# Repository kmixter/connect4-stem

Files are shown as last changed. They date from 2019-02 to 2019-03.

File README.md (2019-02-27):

# README #

This repository is the software and 3D part source for a "Connect-4" STEM project.

### Parts to purchase ###

* Purchase [wooden Connect Four game](https://www.target.com/p/connect-4-rustic-series-board-game/-/A-52118927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) for $19
* Purchase [aluminum slider](https://www.sparkfun.com/products/12500) for $12
* Purchase [channel slider](https://www.sparkfun.com/products/12560) for $5
* Purchase 2 [ball bearings](https://www.sparkfun.com/products/13277) for $2
* Purchase [stepper motor](https://www.amazon.com/gp/product/B00EYIFW70/ref=ppx_yo_dt_b_asin_title_o07__o00_s00?ie=UTF8&psc=1) for $17
* Purchase [Induino Mega](https://www.amazon.com/gp/product/B01G6Z1EYI/ref=ppx_yo_dt_b_asin_title_o04__o00_s00?ie=UTF8&psc=1) for $14 (or any Arduino Mega compatible board)
* Purchase [Adafruit motor shield](https://www.amazon.com/gp/product/B00PUTH3B0/ref=oh_aui_search_asin_title?ie=UTF8&psc=1) for $19
* Purchase [Timing belt, pulley, and tensioner](https://www.amazon.com/gp/product/B07FYYGFGQ/ref=ppx_yo_dt_b_asin_title_o09__o00_s00?ie=UTF8&psc=1) for $13
* Purchase [Stacking headers](https://www.amazon.com/gp/product/B00LB76EVU/ref=ppx_yo_dt_b_asin_title_o00__o00_s00?ie=UTF8&psc=1) for $6
* Purchase [Ribbon cable](https://www.amazon.com/gp/product/B01D9KISHY/ref=ppx_yo_dt_b_asin_title_o09__o00_s01?ie=UTF8&psc=1) for $8
* Purchase [LCD screen](https://www.amazon.com/gp/product/B01E6N19YC/ref=ppx_yo_dt_b_asin_title_o07__o00_s00?ie=UTF8&psc=1) for $10
* Purchase [Servo](https://www.amazon.com/gp/product/B07C5PGD3Q/ref=oh_aui_search_asin_title?ie=UTF8&psc=1) for $11
* Purchase 7 [photo interrupters](https://www.digikey.com/product-detail/en/sharp-socle-technology/GP1A57HRJ00F/1855-1043-ND/718287) for $28
* Purchase [red](https://www.adafruit.com/product/1445) and [green](https://www.adafruit.com/product/1504) momentary pushbuttons for $2
* Purchase 7 330ohm 1/4w resistors
* Purchase a micro-switch
* Purchase a [battery and charger](https://www.overstock.com/Emergency-Preparedness/Large-Capacity-9800MAH-DC12V-Portable-Rechargeable-Li-ion-Battey-Pack/17432557/product.html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) for $30

* You will need a 3D printer and filament. We used ABS, though presumably PLA also works.
* You will also want wood screws of various sizes and metal bolt/nut combos, mostly of 3mm size.
* For nicer connections, you'll also want to consider soldering iron/solder, heat shrink, and a Dupont connector kit.

### Construction of robot ###

The following parts are all available here print. They can be printed on
an inexpensive hobbyist 3D printer with a 150mm x 150mm x 150mm printing
volume. We used ABS filament for durability and easy in welding pieces
together with acetone. No acrylic parts are needed.

These are the parts for the gantry dropper mechanism above the board:

* [gantry hopper holder](parts/PatrickMcCabe/Piece Holder.STL)
* [2x belt clamp](parts/PatrickMcCabe/Belt Clamp.STL)
* [gantry slider top](parts/PatrickMcCabe/Slider Top.STL)
* [2x bearing block](parts/PatrickMcCabe/Bearing Block.STL)
* [Motor mount](parts/PatrickMcCabe/Motor Mount.STL)
* [Combined idler and post](parts/combined-idler-post.stl)
* [Disc Funnel](parts/PatrickMcCabe/Slider Spacer Front.STL)
* [Servo Releaser](parts/thinner-servo-releaser.stl)
* [Disc hopper](parts/taller-gantry-hopper.stl)

To build the gantry, which is the slider that slides across the top of
the board and drops discs into the board:

* Connect the stepper motor to the Motor Mount with screws.
* Connect the motor mount to the 15" C channel in the second to left-most
  screw holes.
* Insert the bearings into the two bearing blocks. This is a very tight
  fit. I used a pair of pliers to squeeze the bearing into the block to be
  flush. This damaged one of my bearings and I needed to purchase a new one.
  Be careful to only squeeze the outermost ring of the bearing to avoid bending
  the internal mechanism and causing friction when the bearing moves.
* Insert the combined idler and rod into the two bearings.
* Screw the two bearing blocks into the C channel, aligned with the rightmost
  screw holes. The bearing blocks did not fit well into the channel and would
  cause the channel to bend outward and increase the friction of the slider
  against the channel. I ended up significantly sanding down the two bearing
  blocks so they fit into the channel without bending it. Sorry I did not get
  around to redesigning the parts to be smaller. Likely they are about 1mm too
  thick.
* Place the C clamps on the C-channel.
* Screw the top of the C clamps into the gantry slider top.
* Screw the front of the C clamps into the disc funnel.
* Screw the gantry hopper holder into the left side of the C clamps.
* Screw the servo onto the top of the gantry slider top.
* Cut the servo arm to be less than 4mm and screw the Servo Releaser
  into the servo arm.
* Superglue the servo arm onto the servo drive to avoid accidental disloding.
* Screw the gantry hopper into the gantry hopper holder.
* Attach the belt pulley to the stepper motor with set screw included with
  pulley.
* Wrap the belt drive around the idler and the stepper pulley, pull moderately tight.
* Cut belt to 15cm longer than distance to gantry slider top.
* Route the top sides of the belt loop up into the gantry slider top, pulled around
  to the outside of the gantry slider top.
* Clamp down the belt drive with 2 Belt Clamps and 4 screws.
* Tighten the belts with spring tensioners.
* Connect the microswitch to the C channel. See picture for positioning.
* Consider soldering a 3-pin connector like that shown to the microcontroller
  to make it easier to take the device apart in the future.

At this point the next best step is to attach the 7 photo-interrupters to
the top of the board. This is probably the most labor intensive step. Each
photo-interrupter has an emitter side (2 pins) and a phototransistor side (3
pins). On both sides longest lead is ground. The middle lead of the phototransistor
is the output. The other lead is VCC. Since the emitter is just a simple
IR LED, current limiting is required to avoid burning out the LED. Each
LED power needs a 330V 1/4W resistor between it and actual 5V input. The
phototransistor is actually a complicated circuit and does not need current
limiting.

The photo-interrupters come with emitter and receiver sides connected by a
plastic spacer. This spacer is similar to the width of the Connect 4 board,
so it is tempting to think they can just be used as is. However, the spacer
is too thick and discs will not fit through the spacers (they would leave
less than 1 1/4" wide, the diameter of the discs). As such, the photo-interruptors
call be cut easily with wire cutters to give full access to the drop area
at the top of the board.

But before cutting the photo-interrupters they should be wired up and attached
to the board. In my case I put the phototransistor side at the back of the board
(since we need 7 signal wires coming out from the back of the board, which is
unsightly), and emitter side at the front. For the emitter and phototransistors,
the same GND and 5V wires were used. These wires plus the 7 signal wires come
from the same ribbon cable. For convenience I used white wire for 5V, black for GND,
and purple through brown for the 7 columns, using 9 of the 10 wires of the 10-wire
ribbon cable. Additionally, the 5V and GND side of the microswitch and its output
should be connected to this cable. The output signal should be wired to gray.

A bus wire was used to solder all GND connections together. On the emitter side
since all emitters require 330ohm biasing resistors I used heat-shrink to hide
the resistors and insulate the 5V wire which was chained between each emitter
positive side.

To reduce surplus wiring in this visible part of the board, I used a paper template
of the top of the board, with exact markings of each column and spaced, soldered,
and heat-shrunk the wires for the photo-interruptors. The spacer of the
photo-transistors was still intact at this stage. Finally when all wires were
intact and connected to the 10-wire ribbon cable, the spacers were cut for all 7
interruptors. The photo-interrupters were then glued to the top of the board
with a hotglue gun. When glued, make sure that the emitter and receiver sides of
the photo-interrupters are as flush as possible with the opening of the board.
If they are too wide, discs can get stuck on the top of the board when they pass
them. If they are too narrow, discs can get stuck on top of the photo interrupter.
Any excess glue towards the inside of the board can be clipped away for a smooth
transition from the funnel, past photo-interrupter, into the board.

Next the feet and slide should be printed and attached to the board.

Print these parts:

* [back-right foot](parts/foot.stl)
* [back-left battery-holder foot](parts/battery-foot.stl)
* [front-left controller foot](parts/controller-foot.stl)
* [front-right hopper-foot](parts/hopper-foot.stl)
* [controller top](parts/controller-top.stl)
* [Slide left](parts/slide-left.stl)
* [Slide right](parts/slide-right.stl)

Use acetone to weld the slide left and slide right pieces together into one
large 25cm wide piece.

Each foot connects at the bottom of the foot and optionally on the sides
with a screw. Drill pilot holes into the connect4 board. Try to make the
feet of the two sides as close to flush and level with each other as possible.

Connect the battery mount to the back left, controller mount to front left,
disc holder foot to front right, and regular foot to back right. Once these
are well secured by screws, attach the slide on top of the feet. Screw the slide
into place. The cutout at the back of the slide may be too small for the connect4
board latch that closes the bottom of the board so the discs don't fall out.
If so, use a file or sandpaper to make it wide enough to give proper clearance.

At this point you will want to wire up the controller box. Place the I2C LCD
panel onto the spacer rods inside the controller box. Use another 10-lead ribbon
cable, using black for GND and white for 5V. Use gray and purple leads for
I2C SDA and SDL signals. Use green for yes button signal and red for no button
signal. The other wires can go unused. Insert the momentary pushbuttons into
the controller top piece. For future maintenance you may want to solder each
of these buttons to connectors when then connect to the ribbon cable wires.
The "signal" for the momentary push-buttons is actually a ground pull-down.
This means the push-buttons should be wired to GND on one side and the other
is the "signal" back to the GPIO pins. The GPIO pins will be configured in
pull-up mode so that they read 5V when button is not pressed and 0V/GND when
pressed.

Leave roughly 15cm for this ribbon cable. Put a dupont female 4-pin end on
the black through purple wires. Put a 2 pin end up the red and green wires.

Screw the controller top into the controller foot.

Finally, insert the battery into the battery holder, with the power plugs
oriented to the front bottom and the LED and switch oriented to the back
bottom of the battery holder. Pull the battery connectors out so they are coming
towards the controller foot.

At this point the base is stable enough to put the gantry on the board.

These are the parts for connecting the gantry to the board:

* [Left gantry connector](parts/gantry-connector-left.stl)
* [Right gantry connector](parts/gantry-connector-right.stl)

To attach the gantry to the board:

* Align the connectors to the very top of the wooden legs of the Connect-4 board.
* Level both the left and right connectors.
* Carefully align the gantry with the top of the board. Several things to keep
  in mind. There needs to be enough vertical clearance for the C sliders to
  not touch the photo-interruptor plastic or any of the wires connecting to it.
  Try placing discs through the funnel and make sure they clear the edges of the
  photo-interruptors and the board.
* Once aligned, carefully drill a 1/8" hole through the screw-holes in the bottom
  of the C channel and the left and right gantry connectors. To reduce potential
  for the gantry to slip forward and back, squeeze the connectors in towards the
  center of the board slightly when drilling the hole. This will assure the screws
  are slightly pulling the C channel away from the center and this spring will keep
  the gantry from moving forward and back.

Now that the gantry and feet are connected, the final step is wiring up the
Arduino, motor boards, and mounting them in their enclosure.

These are the parts for the enclosure

* [Arduino enclosure bottom](parts/arduino-enclosure-bottom.stl)
* [Arduino enclosure top](parts/arduino-enclosure-top.stl)

Screw the enclosure bottom into the left leg of the connect4 board, positioning
it slightly (~ 1/4 inch) below the left gantry connector. There should be a
ribbon cable passage on the bottom of the enclosure and on the back side
of the enclosure, if oriented properly.

If you received the same adafruit motor board, the motor board needs to have
stacking connectors soldered to it. Solder these connectors.

We are going to need to modify the motor board for three more reasons:

* The display also needs to share the I2C bus and VCC and GND with the motor board
* The controller buttons need to be connected to GPIOs.
* The gantry also needs to share the VCC and GND with the motor board.

To achieve all of these, we get VCC and GND by adding female connectors to the
motor board. We use the blank breadboard in the middle of the motor board to
break out access to D8 (no button) and D9 (yes button).

Screw the Arduino Mega board into the Arduino enclosure bottom.

Route the gantry ribbon cable into the enclosure in the back ribbon cable passage.
Route the controller ribbon cable into the enclosure via the bottom ribbon cable
passage.

Attach gray wire (micro-switch) from gantry ribbon cable to A8, attach the rest
of the gantry wires to A9-A15. The Dupont header you created earlier makes this
an easy connection directly to the Arduino Mega board.

You can now connect the servo to the motor board. Connect the servo 3-pin connector
to the servo extension cable (white extension wire should connect to orange servo
wire). Then route the extension cable through the back ribbon cable passage. Plug
the extension cable into the motor board servo 2 3-pin male connector.

For the controller ribbon cable, attach the I2C cables (gray and purple) to the
female stacking connectors you soldered onto the motor board. Attach the
green and red signal wires from the push button to the D8 and D9 connectors you
soldered on earlier.

Stack the motor board on top of the arduino board.

Finally, take the Arduino enclosure top and slide it onto the Arduino enclosure
bottom.

### Building code ###

At this point you are ready to start building and running code.

Clone this repository into $HOME/prj/connect4-stem

Install the arduino SDK. For simplicity install it to $HOME/prj/arduino-1.8.8.
If the version number is different or you decide to install it to a different
directory, you will just need to either modify the Makefile or pass a different
ADIR variable into the make command.

You will need to have installed host compiler tools such as g++ and terminal
emulator picoterm.

```
$ sudo apt-get install g++ picoterm
```

Now begin to build:

```
$ cd $HOME/prj/connect4-stem/src
$ make
```

Note that this makefile uses the Arduino SDK command-line tools directly.
Using .ino and .dce files is convenient for beginners using Arduino GUI.
However to support unit testing and building the same code on host, a
more powerful build environment is needed. This makefile builds binary,
converts it to flashable version and then ultimately flashes it to device.

Just running make will cause host versions and arduino versions of code to be
built. The host versions allow us to unit test various code before it is
put on device. The unit tests will automatically run and device code will
only be built if the unit tests succeed (which they should in any clean
checkout).

To first run code on Arduino, do the follow:

* Make sure your host computer is connected to Arduino by USB
* Make sure battery is charged and plugged into Arduino and turned on.

```
$ make run
```

The code will be built and flashed to the Arduino. The make command will now
run picoterm to show serial output from the code.

IMPORTANT: Never flash another program to Arduino unless you really know
what you are doing! This is because you have now connected various digital
GPIOs and analog GPIOs to be inputs and outputs. If you flash different
code that changes input pins to output pins, you run the risk of shorting
the Arduino Mega board, and may need to replace it.

### Testing ###

Besides the unit test, the Arduino code has diagnostic mode. When showing
"Do you want to play?" you can push both yes and no buttons simultaneously
and a diagnostic mode will be entered. This allows you to run a dropper test.
This test will find the home position (step backwards until "home" microswitch
is pressed by the slider), advance forward to each column in succession,
use the servo to drop the disc into the column, wait for the disc to pass
the photo-interrupter. After a disc is placed into each of the 7 columns
successfully the test is complete. When this test completes you can be
moderately assured that the game mode will work.

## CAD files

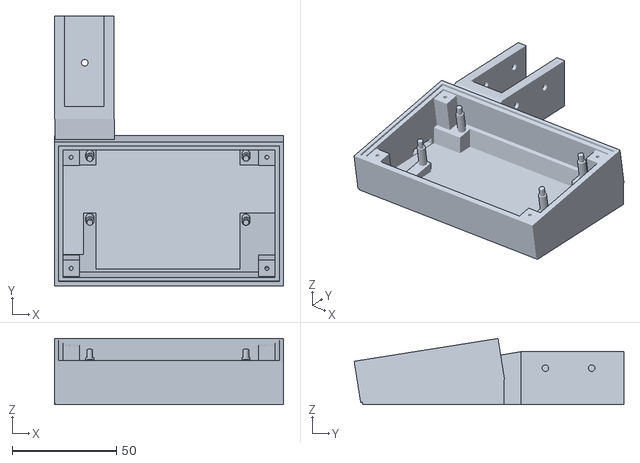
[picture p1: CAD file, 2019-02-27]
parts/controller-foot.stl
110.0 x 129.6 x 31.7

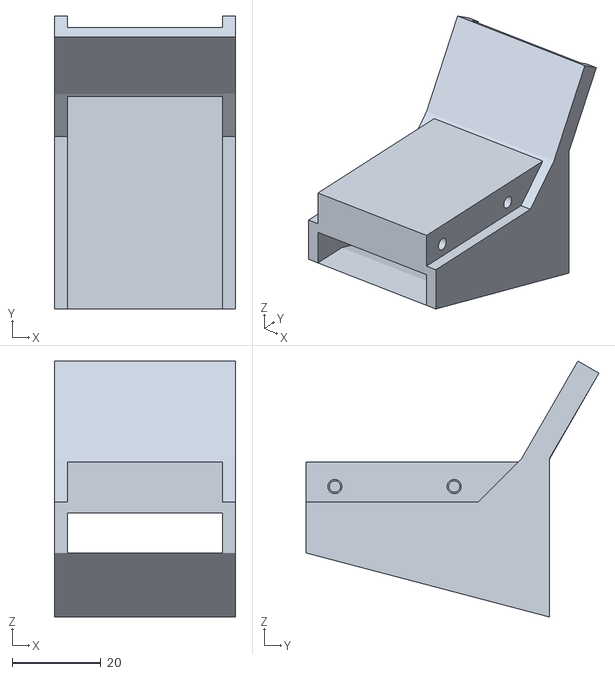
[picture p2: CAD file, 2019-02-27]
parts/PatrickMcCabe/Slider Spacer Front.STL
41.0 x 66.2 x 57.9

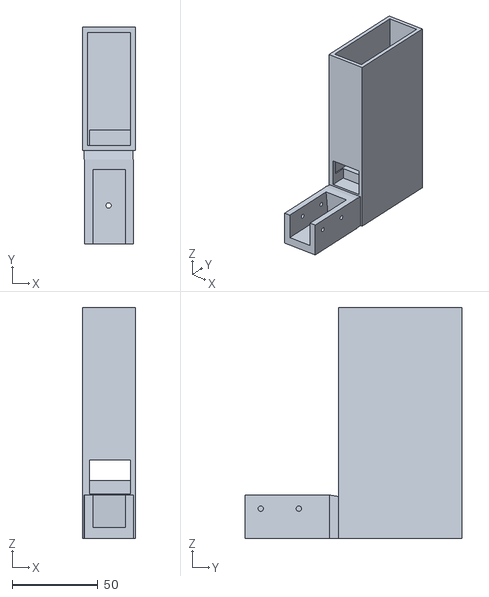
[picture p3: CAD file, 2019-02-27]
parts/battery-foot.stl
31.0 x 126.6 x 135.0

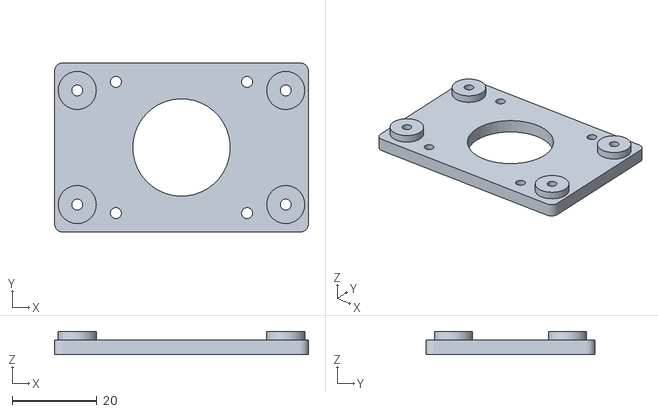
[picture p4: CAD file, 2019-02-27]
parts/PatrickMcCabe/Motor Mount.STL
60.0 x 40.0 x 5.50

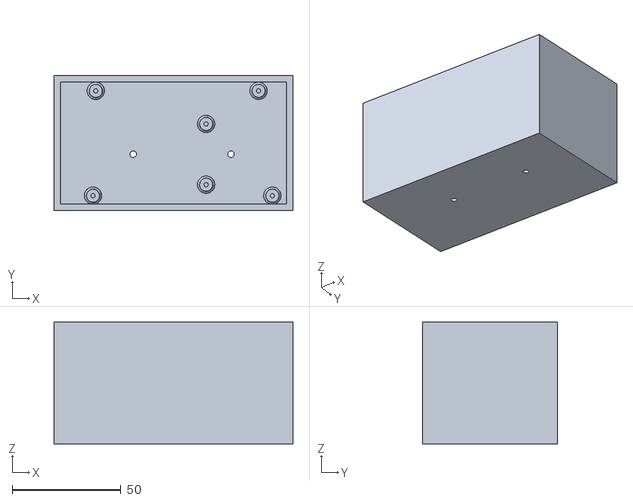
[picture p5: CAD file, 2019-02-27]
parts/arduino-enclosure-bottom.stl
110.0 x 62.0 x 56.0

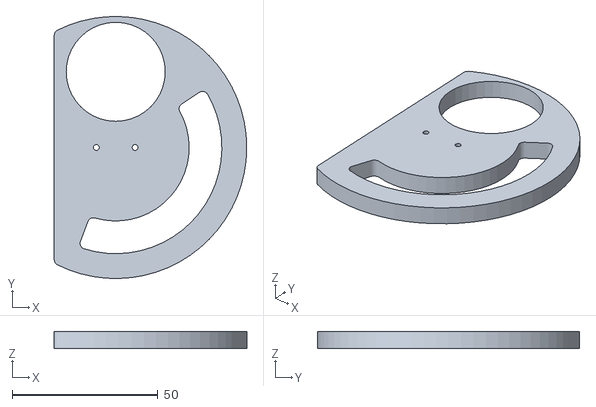
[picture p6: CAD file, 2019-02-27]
parts/PatrickMcCabe/Servo Releaser.STL
66.1 x 90.0 x 6.00

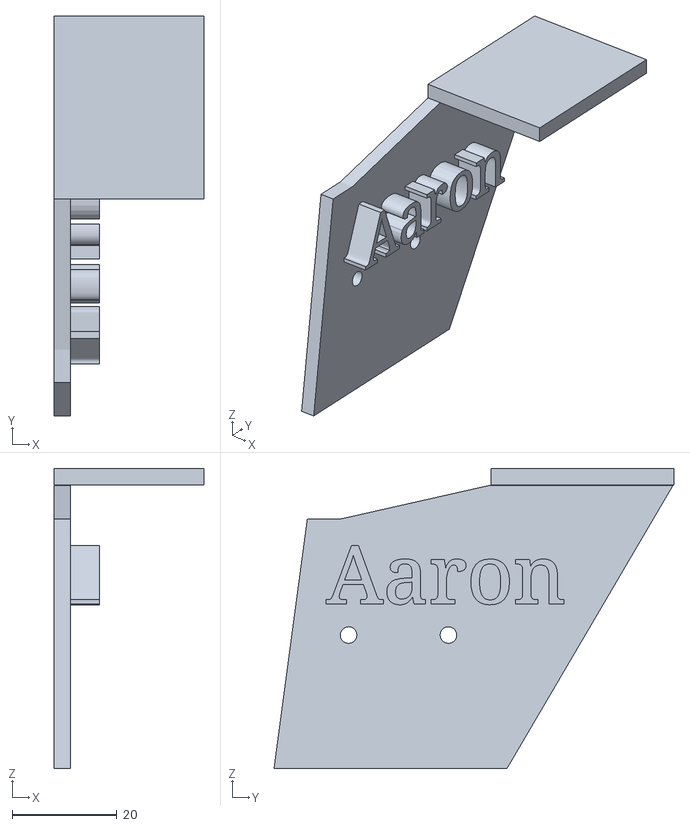
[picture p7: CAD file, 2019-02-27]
parts/gantry-connector-right.stl
28.6 x 76.3 x 57.3

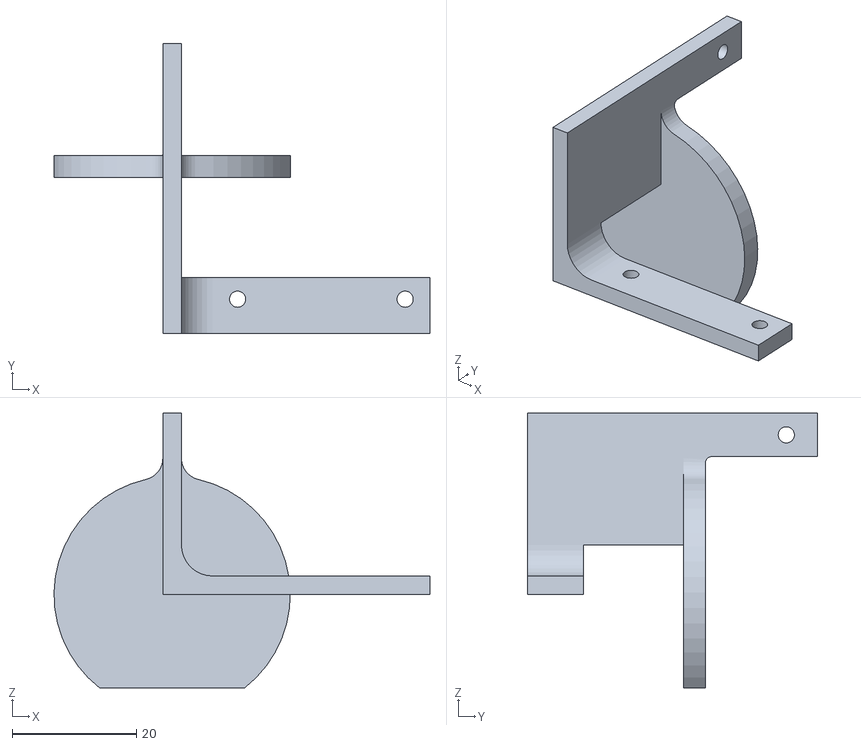
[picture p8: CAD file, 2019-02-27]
parts/PatrickMcCabe/Piece Holder.STL
60.5 x 46.6 x 44.2

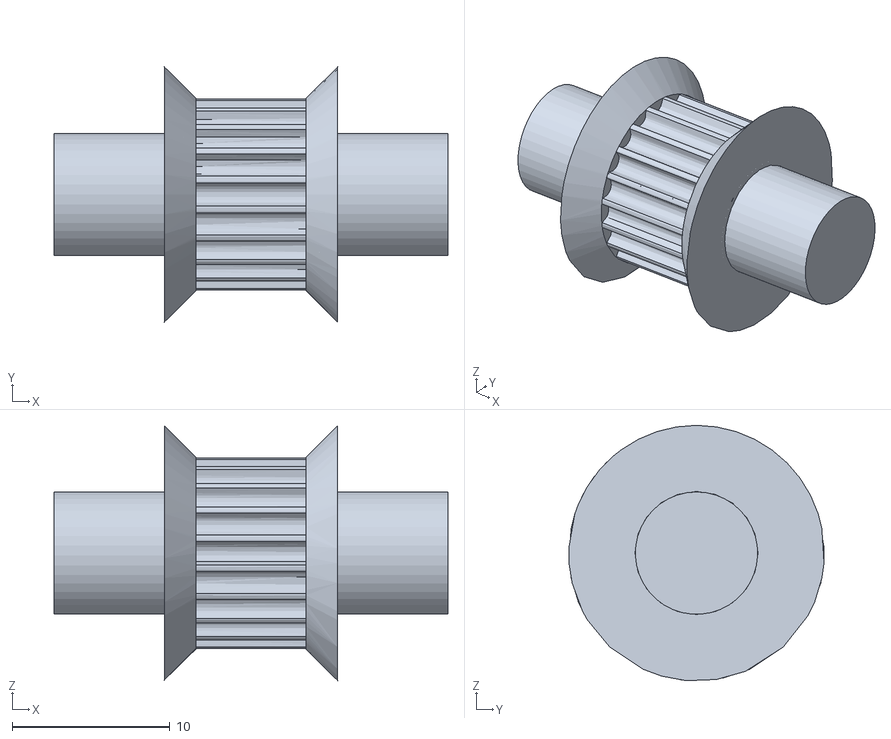
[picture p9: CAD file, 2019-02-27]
parts/combo-idler-post.stl
25.0 x 16.2 x 16.2

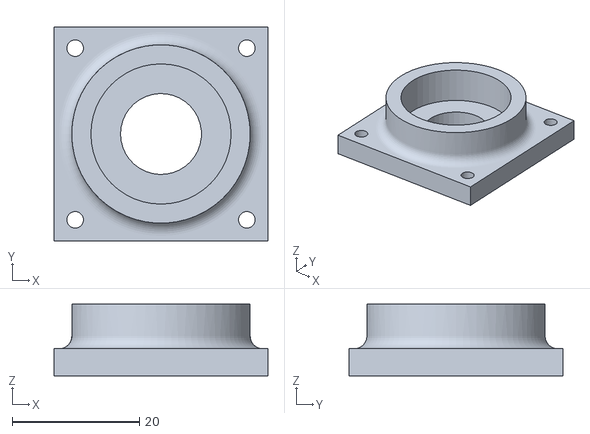
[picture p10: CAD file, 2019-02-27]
parts/PatrickMcCabe/Bearing Block.STL
33.6 x 33.6 x 11.3

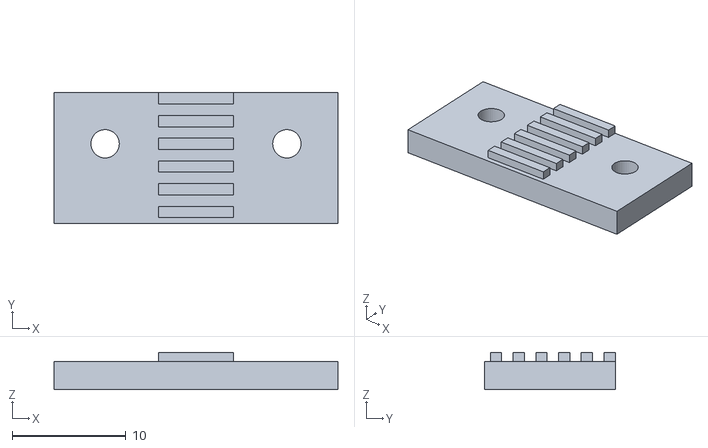
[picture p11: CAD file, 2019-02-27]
parts/PatrickMcCabe/Belt Clamp.STL
25.0 x 11.5 x 3.30

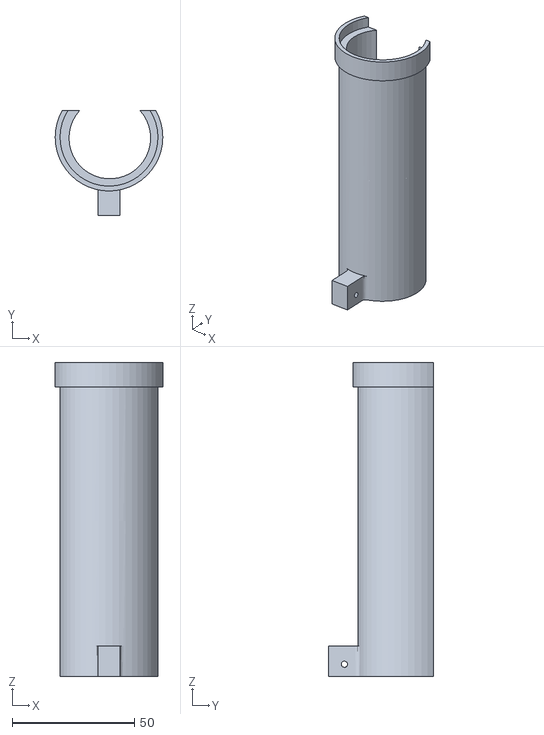
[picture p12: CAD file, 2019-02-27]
parts/taller-gantry-hopper.stl
44.0 x 42.9 x 128.3

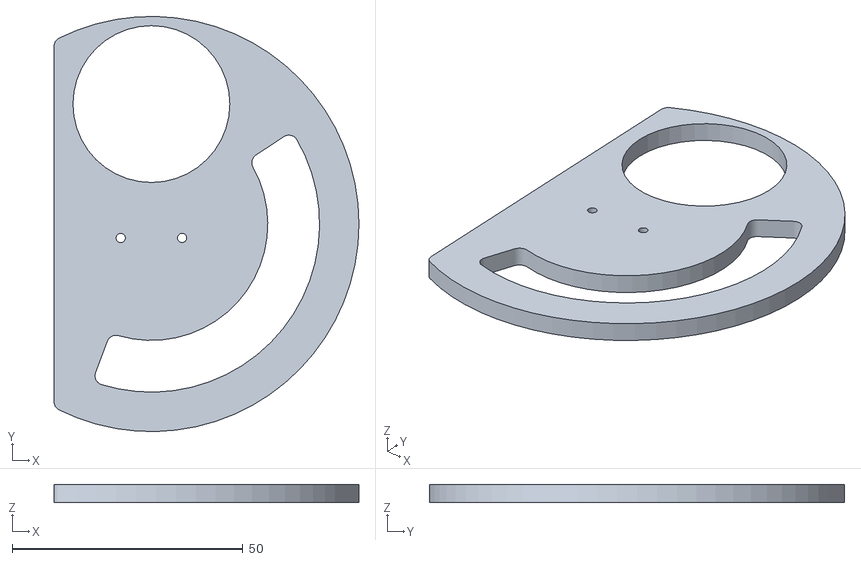
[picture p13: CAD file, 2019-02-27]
parts/thinner-servo-releaser.stl
66.1 x 90.0 x 4.00

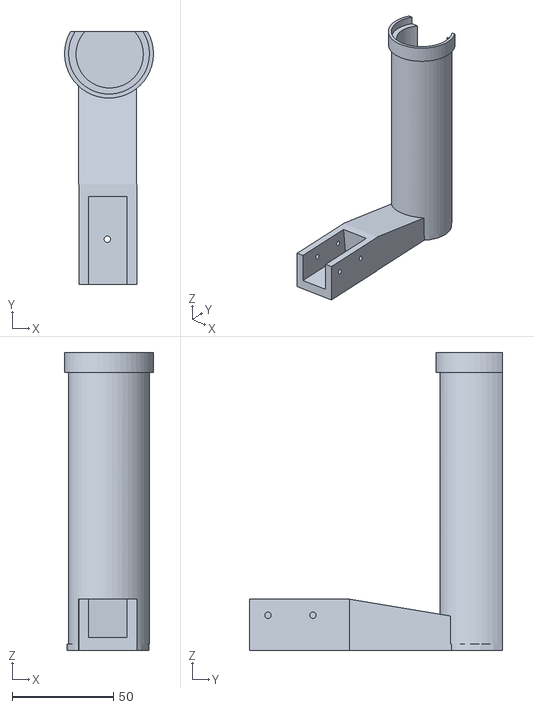
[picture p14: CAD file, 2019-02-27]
parts/hopper-foot.stl
44.0 x 125.0 x 147.3

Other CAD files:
parts/arduino-enclosure-top.stl
parts/gantry-connector-left.stl
parts/controller-top.stl
parts/foot.stl
parts/slide-left.stl
parts/slide-right.stl

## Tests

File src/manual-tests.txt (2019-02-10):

1. Press button while superbot is thinking. Verify asks if last move
   was right, or fails out if first.
2. No at play game.
3. No to cycle through each game.
4. Move after 2 seconds, verify tracks new board position.
5. Test user wins (with random bot)
6. Test bot wins (with rule3 bot)
7. Test max bot starts ok
8. Insert disc during first move fails out
9. Test empty hopper with first drop
10. Press bot during settling of rule3 bot
11. Test button during first move asks to quit, no continues move
12. Test drop during first move bails

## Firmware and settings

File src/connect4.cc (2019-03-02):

#include <Arduino.h>
#include <Adafruit_MotorShield.h>
#include <Wire.h> 
#include <LiquidCrystal_I2C.h>

#include "display_controller.h"
#include "dropper_controller.h"
#include "input_manager.h"
#include "prng.h"
#include "maxbot.h"
#include "rule3bot.h"
#include "randombot.h"

LiquidCrystal_I2C g_lcd(0x27,20,4);  // set the LCD address to 0x27 for a 16 chars and 2 line display
const int kShowMessageTimeoutMs = 2500;

typedef void (*StateHandler)();
StateHandler g_state = nullptr;

InputManager g_input;
DropperController g_dropper;

const unsigned long kUserSwitchColumnTimeoutMs = 2000;
static const char kExitGameEarly[] = "End game early?";

DisplayController g_display;
char g_string[64];

SmallPRNG g_prng(0);
RandomBot g_randombot(kRedDisc, &g_prng);
Rule3Bot g_rule3bot(kRedDisc, &g_prng);
MaxBotConstantEvals g_maxbot(kRedDisc, 2500, &g_prng, true);

void setup()
{
  // Start serial connection
  Serial.begin(115200);

  g_display.Initialize(&g_lcd);
  g_dropper.Initialize(&g_input);
}

enum YesNoResponse {
  kYesNoResponseNo,
  kYesNoResponseYes,
  kYesNoResponseBothButtons
};

YesNoResponse AskYesNo(const char* question, bool blink = false,
                       bool allow_both_buttons = false) {
  g_display.Show(question);
  InputEvent e;
  unsigned long last_ms = millis();
  const int kBlinkIntervalMs = 500;
  bool display_on = true;
  bool yes_down = false, no_down = false, both_down = false;

  while (true) {
    yield();
    if (blink && millis() - last_ms > kBlinkIntervalMs) {
      display_on = !display_on;
      if (display_on)
        g_lcd.backlight();
      else
        g_lcd.noBacklight();
      last_ms = millis();
    }
    if (!g_input.Get(&e))
      continue;
    if (e.IsKeyUp(kYesButtonKey)) {
      g_lcd.backlight();
      yes_down = false;
      if (!(allow_both_buttons && both_down))
        return kYesNoResponseYes;
    }
    if (e.IsKeyUp(kNoButtonKey)) {
      g_lcd.backlight();
      no_down = false;
      if (!(allow_both_buttons && both_down))
        return kYesNoResponseNo;
    }
    if (allow_both_buttons && both_down && !yes_down && !no_down) {
      return kYesNoResponseBothButtons;
    }
    if (e.kind == kKeyDown) {
      if (e.IsKeyDown(kYesButtonKey))
        yes_down = true;
      if (e.IsKeyDown(kNoButtonKey))
        no_down = true;
      if (yes_down && no_down)
        both_down = true;
      continue;
    }
    Serial.print("Ignoring key ");
    Serial.println(e.key);
  }
}

void WaitForUp(const InputEvent& down) {
  InputEvent e;
  while (true) {
    yield();
    if (g_input.Get(&e)) {
      if (e.IsKeyUp(down.key))
        return;
    }
  }
}

void DumpBoardToSerial(Board* b, const char* desc) {
  Serial.println(desc);
  for (int row = 5; row >= 0; --row) {
    for (int col = 0; col < 7; ++col) {
      switch (b->Get(row, col)) {
        case kRedDisc:
          Serial.print("R ");
          break;
        case kYellowDisc:
          Serial.print("Y ");
          break;
        default:
          Serial.print("_ ");
          break;
      }
    }
    Serial.println("");
  }
}

void ShowMessage(const char* msg) {
  g_display.Show(msg);
  delay(kShowMessageTimeoutMs);
  g_input.Flush();
}

struct UserMove {
  UserMove() : column(-1), row(-1), selection_ms(0), done_showing(false) {}

  bool IsSet() const {
    return column >= 0;
  }

  bool IsSettled() const {
    return millis() - selection_ms >= kUserSwitchColumnTimeoutMs;
  }

  void Reset() {
    column = -1;
    row = -1;
    selection_ms = 0;
    done_showing = false;
  }

  int column;
  int row;
  unsigned long selection_ms;
  bool done_showing;
};

void UndoUserMove(Board* b, UserMove* user_move) {
  if (!user_move->IsSet())
    return;
  b->UnAdd(user_move->column);
  user_move->Reset();
}

void ShowUserMove(PlayerBot* bot, Board* b, UserMove* user_move) {
  if (user_move->IsSet() && !user_move->done_showing) {
    strcpy(g_string, "You moved to ");
    strcat(g_string, Board::GetCellLocator(user_move->row, user_move->column));
    g_display.Show(g_string, true);
    if (user_move->IsSettled())
      user_move->done_showing = true;
  } else {
    strcpy(g_string, bot->GetName());
    strcat(g_string, " is thinking");
    g_display.Show(g_string, true);
    g_display.UpdateBoardBitmap(b->GetBitmap());
  }
}

enum BotResult {
  kBotMoved,
  kBotTurnUserDoOver,
  kBotSignalExit,
  kBotContinue
};

class InterruptableObserver : public SimpleObserver {
 public:
  InterruptableObserver() {}

  bool Observe(PlayerBot::Observer::State* s) {
    InputEvent e;
    yield();
    if (g_input.Peek(&e)) {
      Serial.println("Interruption during observer");
      return false;
    }
    if (s->kind == kHeuristicDone) {
      ++heuristics_computed;
      if (heuristics_computed % 200 == 1) {
        Serial.println("200 more heuristics");
      }
    } else if (s->kind == kMoveDone) {
      heuristic = s->heuristic;
      return SimpleObserver::Observe(s);
    }
    return true;
  }
  void Reset() {
    heuristics_computed = 0;
  }

  int heuristic = 0;
  int heuristics_computed = 0;
};

BotResult HandleKeyDuringBotTurn(Board* b, InputEvent* e,
                                 UserMove* user_move) {
  switch (e->key) {
    case kYesButtonKey:
    case kNoButtonKey: {
      if (e->kind == kKeyDown)
        WaitForUp(*e);
      if (user_move->IsSet()) {
        strcpy(g_string, "Was ");
        strcat(g_string, b->GetCellLocator(user_move->row, user_move->column));
        strcat(g_string, " your last move?");
        if (!AskYesNo(g_string)) {
          UndoUserMove(b, user_move);
          g_display.Show("Realigning, please wait...");
          if (!g_dropper.MoveToColumn(g_dropper.GetClosestColumn())) {
            ShowMessage("Sorry, too many mistakes.");
            return kBotSignalExit;
          }
          return kBotTurnUserDoOver;
        }
      } else {
        if (AskYesNo(g_string)) {

        }
      }
      if (AskYesNo(kExitGameEarly)) {
        return kBotSignalExit;
      }
      return kBotContinue;
    }

    case kHomeSwitchKey: {
      ShowMessage("Home key pushed. Failed.");
      return kBotSignalExit;
    }

    case kColumn0Key:
    case kColumn1Key:
    case kColumn2Key:
    case kColumn3Key:
    case kColumn4Key:
    case kColumn5Key:
    case kColumn6Key: {
      if (e->kind == kKeyUp) {
        // We have already somehow consumed the up event for the column,
        // which is a problem because we need the user handler to consume
        // this. Fail out. Hopefully this won't happen.
        Serial.println("Up event for column");
        break;
      }
      if (user_move->IsSet()) {
        // User moves while the bot is thinking/moving. Let's assume they aren't
        // cheating and they moved their disc from where we thought
        // they last put it.
        UndoUserMove(b, user_move);
        return kBotTurnUserDoOver;
      }
      break;
    }
    case kKeyMax: // avoid warning.
      break;
  }
  ShowMessage("I am confused! Ending game.");
  return kBotSignalExit;
}

BotResult HandleBotTurn(Board* b, PlayerBot* bot, CellContents disc,
                        UserMove* user_move) {
  int bot_row;
  InputEvent e;
  InterruptableObserver o;

  while (true) {
    o.Reset();
    ShowUserMove(bot, b, user_move);
    g_display.UpdateBoardBitmap(b->GetBitmap());
    unsigned long bot_start_ms = millis();
    DumpBoardToSerial(b, "Bot board");
    bot->FindNextMove(b, &o);
    if (o.success) {
      Serial.print("Bot took ");
      Serial.print(millis() - bot_start_ms);
      Serial.print("ms and computed ");
      Serial.print(o.heuristics_computed);
      Serial.print(" heuristics, final ");
      Serial.println(o.heuristic);
      break;
    }
    if (!g_input.Peek(&e)) {
      ShowMessage("Bot failed.");
      return kBotSignalExit;
    }
    Serial.println("Handling PlayerBot interrupt");
    while (g_input.Get(&e)) {
      BotResult r = HandleKeyDuringBotTurn(b, &e, user_move);
      if (r != kBotContinue)
        return r;
    }
  }

  if (!b->Add(o.column, disc, &bot_row)) {
    ShowMessage("Bot failed.");
    return kBotSignalExit;
  }
  // Now remove the chip until we really have placed it.
  b->UnAdd(o.column);

  // Continue waiting for the user's move to settle (enough time to pass).
  // We promise to give the user a settle time to drop their disc and
  // move their hand away before we move the dropper. If we are running a
  // slow bot, enough time will have already passed.
  while (!user_move->IsSettled()) {
    yield();
    if (g_input.Peek(&e)) {
      BotResult r = HandleKeyDuringBotTurn(b, &e, user_move);
      if (r != kBotContinue)
        return r;
    }
  }

  bool successful_move = false;

  while (!successful_move) {
    strcpy(g_string, bot->GetName());
    strcat(g_string, " picks ");
    strcat(g_string, b->GetCellLocator(bot_row, o.column));
    g_display.UpdateBoardBitmap(b->GetBitmap());
    g_display.Show(g_string, true);

    if (!g_dropper.MoveToColumn(o.column) || !g_dropper.DropAndWait()) {
      if (g_input.Get(&e)) {
        BotResult r = HandleKeyDuringBotTurn(b, &e, user_move);
        if (r != kBotContinue)
          return r;
      } else {
        if (AskYesNo("Refill the hopper. Ready?")) {
          g_dropper.Reset();
        } else {
          ShowMessage("Quitting.");
          return kBotSignalExit;
        }
      }
      continue;
    }
    Serial.print(millis());
    Serial.println(", drop finished");
    successful_move = true;
  }

  if (!b->Add(o.column, disc)) {
    ShowMessage("Bot failed post");
    return kBotSignalExit;
  }
  return kBotMoved;
}

void ShowUserPrompt(Board* b) {
  if (b->GetCount() == 0) {
    g_display.Show("You go first.");
  } else {
    g_display.Show("Your turn!", true);
  }
  g_display.UpdateBoardBitmap(b->GetBitmap());
}

bool HandleUserTurn(Board* b, PlayerBot* bot, CellContents disc, UserMove* user_move) {
  InputEvent e;
  DumpBoardToSerial(b, "Your board");
  ShowUserPrompt(b);
  user_move->Reset();

  while (!user_move->IsSet()) {
    yield();
    if (!g_input.Get(&e))
      continue;
    if (e.kind == kKeyDown) {
      int column = e.key - int(kColumn0Key);
      Serial.println("Showing immediate board update");
      if (column >=0 && column <= kColumn6Key && b->Add(column, disc)) {
        g_display.UpdateBoardBitmap(b->GetBitmap());
        b->UnAdd(column);
      }
      continue;
    }

    switch (e.key) {
      case kYesButtonKey:
      case kNoButtonKey:
      case kHomeSwitchKey:
        if (AskYesNo(kExitGameEarly))
          return false;
        ShowUserPrompt(b);
        break;

      case kColumn0Key:
      case kColumn1Key:
      case kColumn2Key:
      case kColumn3Key:
      case kColumn4Key:
      case kColumn5Key:
      case kColumn6Key: {
        int user_row;
        int user_column = e.key - kColumn0Key;
        if (!b->Add(user_column, disc, &user_row))
          continue;

        b->UnAdd(user_column);
        user_move->column = user_column;
        user_move->row = user_row;
        user_move->selection_ms = millis();
        g_display.UpdateBoardBitmap(b->GetBitmap());
        ShowUserMove(bot, b, user_move);
        break;
      }

      case kKeyMax:  // avoid warning
        break;
    }
  }

  b->Add(user_move->column, disc);
  return true;
}

void ShowDraw() {
  AskYesNo("It's a draw! Good game! Continue?", true);
}

void ShowUserWins(Board* b) {
  strcpy(g_string, "Good job, you win! ");
  strcat(g_string, b->GetWinLocator());
  strcat(g_string, " Continue?");
  AskYesNo(g_string, true);
}

void ShowBotWins(PlayerBot* bot, Board* b) {
  strcpy(g_string, bot->GetName());
  strcat(g_string, " won!! ");
  strcat(g_string, b->GetWinLocator());
  strcat(g_string, " Continue?");
  AskYesNo(g_string, true);
}

void RunGame(PlayerBot* bot) {
  if (bot == nullptr) {
    ShowMessage("This bot isn't ready");
    return;
  }
  if (!AskYesNo("Is board empty and latched?")) {
    ShowMessage("Empty the board first.");
    return;
  }

  bool robot_turn = AskYesNo("Can I go first?");

  Board b;
  bool is_draw;
  UserMove user_move;

  while (true) {
    if (robot_turn) {
      BotResult bot_result = HandleBotTurn(&b, bot, kRedDisc, &user_move);

      if (bot_result == kBotSignalExit)
        break;

      if (b.IsTerminal(&is_draw)) {
        if (is_draw)
          ShowDraw();
        else
          ShowBotWins(bot, &b);
        return;
      }

    } else {
      if (!HandleUserTurn(&b, bot, kYellowDisc, &user_move))
        return;

      if (b.IsTerminal(&is_draw)) {
        if (is_draw)
          ShowDraw();
        else
          ShowUserWins(&b);
        return;
      }
    }
    robot_turn = !robot_turn;
  }
}

void RunDropperTest() {
  g_display.Show("Here it goes...");
  for (int i = 0; i < 7; ++i) {
    InputEvent e;
    if (!g_dropper.MoveToColumn(i)) {
      if (!g_input.Get(&e)) {
        ShowMessage("Failed");
        return;
      }
      if (e.IsKeyDown(kYesButtonKey) ||
          e.IsKeyDown(kNoButtonKey)) {
        WaitForUp(e);
        if (AskYesNo("Exit test early?")) {
          return;
        }
        --i;
        continue;
      } else {
        Serial.print("Ignoring ");
        Serial.println(e.key);
      }
    }
    if (!g_dropper.DropAndWait()) {
      ShowMessage("Disc never fell. Empty? Stuck?");
      return;
    }
  }
  ShowMessage("Test passed!");
}

void RunInputTest() {
  g_display.Show("Push button or put disc in column");
  while (g_input.GetCurrentState() != ((1<<kYesButtonKey) | (1<<kNoButtonKey))) {
    InputEvent e;
    bool is_photointerrupter = false;
    yield();
    if (!g_input.Get(&e))
      continue;
    switch (e.key) {
     case kYesButtonKey:
      strcpy(g_string, "Yes button");
      break;
     case kNoButtonKey:
      strcpy(g_string, "No button");
      break;
     case kColumn0Key:
     case kColumn1Key:
     case kColumn2Key:
     case kColumn3Key:
     case kColumn4Key:
     case kColumn5Key:
     case kColumn6Key:
     case kKeyMax: // To avoid warning
      strcpy(g_string, "Column X");
      g_string[7] = 'A' + (int(e.key) - int(kColumn0Key));
      is_photointerrupter = true;
      break;
     case kHomeSwitchKey:
      strcpy(g_string, "Home switch");
      break;
    }
    if (e.kind == kKeyDown)
      strcat(g_string, is_photointerrupter ? " blocked" : " down");
    else
      strcat(g_string, is_photointerrupter ? " clear  " : " up  ");
    g_display.Show(g_string);
  }
  g_display.Show("Exiting");
  delay(2000);
  g_input.Flush();
}

int main(void) {
  init();
  setup();

  struct QuestionBot {
    const char* question;
    PlayerBot* bot;
  } question_bot[] = {
    {
      "Do you want to go easy?",
      &g_randombot
    }, {
      "Do you want to go medium?",
      &g_rule3bot
    }, {
      "Do you want to go hard?",
      &g_maxbot
    }
  };
  int question = 0;
  int num_questions = sizeof(question_bot) / sizeof(question_bot[0]);

  while (true) {
    YesNoResponse yn = AskYesNo("Do you want to play?", false, true);
    if (yn == kYesNoResponseYes) {
      uint32_t seed = micros();
      g_prng.SetSeed(seed);
      Serial.print("Setting PRNG seed to ");
      Serial.println(seed);
      int start_question = question;
      do {
        if (AskYesNo(question_bot[question].question)) {
          RunGame(question_bot[question].bot);
          break;
        } else {
          question = (question + 1) % num_questions;
        }
      } while (question != start_question);
    } else if (yn == kYesNoResponseNo) {
      ShowMessage("Sorry, I don't know any jokes.");
    } else if (yn == kYesNoResponseBothButtons) {
      if (AskYesNo("Run dropper test?"))
        RunDropperTest();
      else if (AskYesNo("Run input test?"))
        RunInputTest();
    }
  }
}

void yield() {
  g_input.Poll();
  if (serialEventRun) serialEventRun();
}

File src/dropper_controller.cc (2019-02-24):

#include "dropper_controller.h"

#include <Arduino.h>

#include "input_manager.h"

const int kStepperStepsPerRevolution = 200;
const int kStepperMotorPort = 2;
const int kServoOutput = 10;
const int kServoLoadingAngle = 0;
const int kServoUnloadingAngle = 80;
const int kStepsAtColumn0 = 20;
const int kStepsBetweenColumns = 170;
const int kDropTimeoutMs = 1000;
const int kErrorTimeoutMs = 5000;
const int kDropDebounceTimeoutMs = 200;
const int kServoRotateTimeMs = 200;
const int kStepMax = kStepsAtColumn0 + 7 * kStepsBetweenColumns;

DropperController::DropperController() : input_(nullptr), current_step_(-1) {
}

void DropperController::Reset() {
  current_step_ = -1;
  MoveServoToUnload(false);
}

void DropperController::Initialize(InputManager* input) {
  input_ = input;

  motors_.begin();

  stepper_ = motors_.getStepper(kStepperStepsPerRevolution, kStepperMotorPort);
  stepper_->setSpeed(10);  // 10 RPM
  stepper_->release();

  Reset();
}

void DropperController::MoveServoToUnload(bool unloading) {
  servo_.attach(kServoOutput);
  servo_.write(unloading ? kServoUnloadingAngle : kServoLoadingAngle);
}

void DropperController::DetachServo() {
  servo_.detach();
}

bool DropperController::MoveToStep(int target_step) {
  if (target_step < kStepsAtColumn0 || target_step > kStepMax) {
    return false;
  }

  if (current_step_ < 0) {
    // First we need to determine our current location.
    Serial.println("Finding home");
    int steps_left = kStepMax + kStepsAtColumn0;

    while (steps_left > 0) {
      yield();
      InputEvent e;
      if (input_->Peek(&e)) {
        if (e.IsKeyDown(kHomeSwitchKey)) {
          Serial.println("Hit home switch, found 0");
          current_step_ = 0;
          input_->Get(&e);
          break;
        } else {
          Serial.print("Interrupted by key during homing, ");
          Serial.println(e.key);
          return false;
        }
      }
      stepper_->step(2, BACKWARD, SINGLE);
      steps_left -= 2;
    }

    if (current_step_ < 0) {
      Serial.println("Couldn't find home.");
      return false;
    }
  }

  Serial.print("Stepping to ");
  Serial.println(target_step);

  while (current_step_ != target_step) {
    yield();
    if (current_step_ < target_step) {
      stepper_->step(1, FORWARD, SINGLE);
      ++current_step_;
    } else {
      stepper_->step(1, BACKWARD, SINGLE);
      --current_step_;
    }
    InputEvent e;
    while (input_->Peek(&e)) {
      if (!e.IsKeyUp(kHomeSwitchKey)) {
        Serial.print("Interrupted by key during move, ");
        Serial.println(e.key);
        return false;
      }
      input_->Get(&e);
    }
  }

  Serial.print("Moved to ");
  Serial.println(current_step_);
  return true;
}

int DropperController::GetColumn() const {
  if (current_step_ < kStepsAtColumn0)
    return -1;
  if ((current_step_ - kStepsAtColumn0) % kStepsBetweenColumns != 0)
    return -1;
  return (current_step_ - kStepsAtColumn0) / kStepsBetweenColumns;
}

int DropperController::GetClosestColumn() const {
  // If either not yet homed or before column 0, assume column 0 is closest.
  if (current_step_ < kStepsAtColumn0)
    return 0;
  int column = (current_step_ - kStepsBetweenColumns) / kStepsBetweenColumns;
  if ((current_step_ - kStepsAtColumn0) % kStepsBetweenColumns >
        kStepsBetweenColumns / 2)
    ++column;
  if (column > 6)
    column = 6;
  return column;
}

bool DropperController::DropAndWait() {
  int this_column = GetColumn();
  if (this_column < 0) {
    Serial.println("Cannot drop when not aligned");
    return false;
  }
  MoveServoToUnload(true);
  stepper_->release();

  unsigned long start_ms = millis();
  InputKey this_key(InputKey(int(kColumn0Key) + this_column));
  InputEvent e;
  bool found = false;

  while (!found && millis() - start_ms < kDropTimeoutMs) {
    yield();
    while (input_->GetFiltered(this_key, &e)) {
      if (e.kind == kKeyUp) {
        Serial.println("Disc passed interrupter");
        found = true;
      }
    }
  }

  // Within a short period of time after dropping the disc, we may
  // get a second enter/exit. Wait for this to pass and consume
  // that event.
  delay(kDropDebounceTimeoutMs);
  while (input_->GetFiltered(this_key, &e)) {
    Serial.println("Consumed interrupter bounce");
  }

  MoveServoToUnload(false);
  delay(kServoRotateTimeMs);
  DetachServo();

  return found;
}

bool DropperController::MoveToColumn(int column) {
  if (column < 0 || column > 6)
    return false;
  return MoveToStep(kStepsAtColumn0 + kStepsBetweenColumns * column);
}

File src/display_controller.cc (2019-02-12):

#include "display_controller.h"

#include <string.h>

#include <Arduino.h>
#include <LiquidCrystal_I2C.h>

#include "board.h"

void DisplayController::Initialize(LiquidCrystal_I2C* lcd) {
  lcd_ = lcd;
  lcd_->init(); 
  lcd_->backlight();
}

void DisplayController::Show(const char* s, bool with_board) {
  int i = 0;
  if (current_ && strcmp(s, current_) == 0)
    return;
  Serial.print("Showing ");
  if (with_board)
    Serial.print("(with board) ");
  Serial.println(s);
  lcd_->clear();
  int max_length = with_board ? 12 : 16;
  for (int l = 0; l < 2; ++l) {
    int line_len = 0;
    int line_start = i;
    int last_break = -1;
    for (; s[i] && line_len < max_length; ++i) {
      if (s[i] == ' ') {
        last_break = i;
      }
      ++line_len;
    }
    if (s[i] == '\0')
      last_break = i;
    else if (last_break < 0)
      last_break = i;
    if (!with_board)
      lcd_->setCursor((16 - (last_break - line_start)) / 2, l);
    else
      lcd_->setCursor(16 - (last_break - line_start), l);
    for (int j = line_start; j < last_break; ++j)
      lcd_->write(s[j]);
    i = last_break;
    if (s[i] == ' ')
      ++i;
  }

  if (with_board) {
    lcd_->setCursor(0, 0);
    for (int i = 4; i < 8; ++i) lcd_->write(i);
    lcd_->setCursor(0, 1);
    for (int i = 0; i < 4; ++i) lcd_->write(i);
  }

  if (current_) free(current_);
  current_ = strdup(s);
}

void DisplayController::UpdateBoardBitmap(uint8_t* bitmap) {
  for (int i = 0; i < 8; ++i) {
    lcd_->createChar(i, bitmap + i * 8);
  }
}

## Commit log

2019-01-04 Initial commit with board.h basically working
2019-01-19 Introduce arduino makefile
2019-01-20 Run both host and Arduino makes
2019-01-20 First version working on device
2019-01-20 Now have start flowchart working
2019-01-20 Building in the motor shield support
2019-01-21 Added servo control, but now nothing works
2019-01-26 Switch to main/yield
2019-01-27 Fix drop debounce problem
    [connect4.cc, dropper_controller.cc]
2019-01-31 Add board case STL
    [board-case-bottom.stl, board-case-top.stl]
2019-02-03 added play_cmd, fixed missing return, not tested on device
    [input_manager.cc]
2019-02-04 Added easy bot and PRNG code, tested on device
2019-02-09 Added interruptable observer
2019-02-10 Allow user to make late changes to board, also add InputManager::Flush
2019-02-10 Fix a number of problems during bot-waiting
    Now we handle inputs during bot turn consistently, before
    we were sometimes dropping out to user's turn incorrectly.
    To fix this, added way to dump current state to serial
    and added -Wall -Werror to all builds (and fixed related
    problems).
    [connect4.cc, dropper_controller.cc]
2019-02-12 Add simple on-display board display
2019-02-15 Fix taunt problem. Overlap showing user move with bot finding move
    [connect4.cc]
2019-02-15 Add optional bottom slide
    [connect4-bottom-slide-left.stl, connect4-bottom-slide-right.stl]
2019-02-21 simplify minimax code, add test for same moves vs board position
2019-02-24 Turn on alphabeta on device - runs 2-3x faster
2019-02-24 Release servo after turn to reduce battery draw
2019-02-27 Added most build instructions and a few more STL files from Patrick project
    [Bearing Block.STL, Belt Clamp.STL, Piece Holder.STL]
2019-02-27 Add remaining STL files and references
    [Motor Mount.STL, Servo Releaser.STL, Slider Spacer Front.STL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]
2019-02-27 Add battery link
2019-03-02 Show you go first correctly
    [connect4.cc]
2019-03-02 Switch to robot goes first by default
